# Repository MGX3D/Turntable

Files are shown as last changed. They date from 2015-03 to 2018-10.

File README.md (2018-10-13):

# MGX3D Automatic Turntable

A high precision rotating platform for 100Kg/250lbs typical loads.

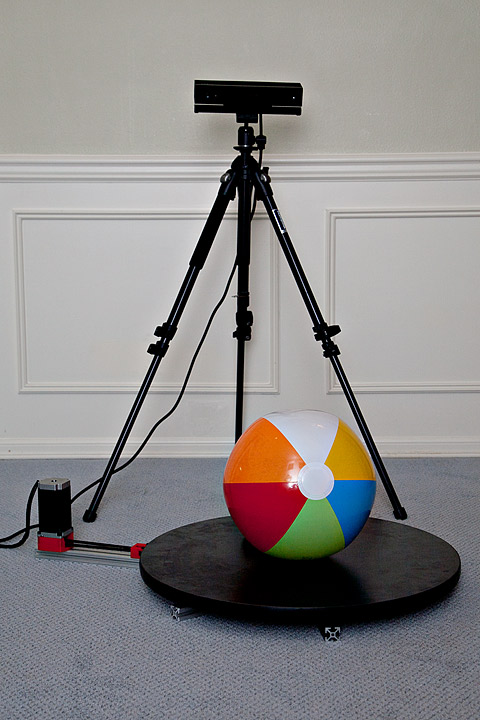
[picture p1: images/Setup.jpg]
Kinect Scan View 3D Scanner view


Description:
------------
This platform was initially designed to automate 3D scanning of people and objects with Kinect v2 and 3D Builder:
- heavy duty: hold a heavy person or average couple, run for 12+ hours non-stop
- powerful drive: spin the person fast enough to avoid scanning artifacts due to movement, breathing, ICD, etc.
- precise rotation: stepper controlled (and USB connected) to experiment with line scanners and algorithms
- low profile: close to the ground increase stability when stepped on
- easy to build: use very few parts that are easy to source
     
The current design has completed more than 2500 scans of people to date, with a typical scan taking only 30 seconds.

Characteristics (typical):
--------------------------
- platform diameter: 500mm (2ft) 
- speed: 0-3 RPM (peripheral speed: 25-50mm/s)
- platform load: up to 300lbs
- resolution: 0.02mm for 450mm OD object (20 arcseconds)

Parts required:
---------------
Warning: not final, might be incomplete. Please be prepared to make adjustments. Unless otherwise noted, eBay/Amazon is a good source for parts.

| Count | Price | Description |
|---|---|---|
| 1x | $40 | 450mm Lazy Susan Aluminum Bearing 500 lbs Turntable Bearings (VXB Brand)|
| 1x | $30 | Stepper motor driver: DM420A. Alternative: HY-DIV268N-5A|
| 1x | $55 | NEMA23, torque: 25 Kg cm (350 oz. in) (example: Wantai 57BYGH115-003 / 3.0A, but many others work here). Alternative is a NEMA17 planetary gear motor (not for Fusion scans!)|
| 4x |  $4 | M5 30mm socket head screws - for the NEMA23 motor mount. Alternative: M4 >35mm and nuts|
| 1x |  $6 | MXL aluminum pulley 40T 8mm bore (anything between 20T and 40T works - bore has to match the motor. GT2 also works)|
| 1x | $10 | 962MXL Timing Belt, .080" Pitch, 77" Outer Circle, 1/4" Wide (McMaster 1679K686, alternative 3/16" 1679K685)|
| 4x |  $3 | F623ZZ: 3x10x4mm flanged bearing for the belt tensioner. Likely to be upgraded to F634zz|
| 2x |  $1 | M3 20mm with 1 nut and 2 washers each. Holds the bearings in the belt tensioner (will be M4 for F634zz)|
| 1x |  $0 | 3D printed part for the NEMA23 mount (STLs in the CAD folder: https://github.com/MGX3D/Turntable/blob/master/CAD/3d_scanner_nema23.stl)|
| 1x |  $0 | 3D printed part for the belt tensioner (STLs in the CAD folder: https://github.com/MGX3D/Turntable/blob/master/CAD/3d_scanner_belt_tensioner.stl)|
| 1x | $20 | Teensy 2.0. Alternative: any Pulse/Dir/Enable capable electronics (examples: Arduino w/ RAMPS shield and shim from Pololu to DM420A or Raspberry Pi 2 with Windows 10 using GPIO pins, etc)|
| 1x | $20 | 1" 8020 72" aluminum extrusion (1010 profile). Will need to be cut in 32"+20"+20". Alternative: metric t-slot extrusion of 20mm or larger|
| 4x |  $4 | 1/4-20 1/2" pan head screws and t-slot nuts - attach the printed parts (motor mount and tensioner) to the aluminum extrusion. Alternative: use M4-12mm + t-nuts|
| 6x |  $5 | M4 16mm screws + t-slot nuts (Can use 8-24 t-slot nuts,  part number 3275 at 8020.inc). Mounts the bearing to the 8020 extrusion|
| 6x |  $1 | #6-1" wood screws - mounts a wooden platform to the bearing. Alternative - double sided tape|
| 1x |  $1 | 2+ meters (6+ feet) of 6 wire cable to transmit signal: low voltage: Enable/Pulse/Direction/Ground (3.3-5vcc) and 12V DC power to the stepper controller. Good fit: network cable with 2 pairs of wires for motor power|
| 1x | $40 |  24" (500mm) disc platform. For 3d scanning of people: preferably 1" thick plywood. Alternative: 1 in. x 24 in. x 2 ft. Pine Edge Glued Panel Round Board at Home Depot (paint or cover with no-slip tape). For other uses: polycarbonate or tempered glass (>3/8", heavy!) or 3/8"-1/2" aluminum disc|
| 12x |  $1 | Optional: M4 washers - only needed if the lazy susan bearing is not offset (inside vs outside rings), example VXB bearings|

--
Approximate total cost: **$250**
Estimated total parts: 37-49

Additional tools required for assembly: 
   - drill with 4mm and 7mm drills. Hand drill works, drill press is better.
   - metric hex/allen keys for metric M3, M4 and M5 screws (m5 works for SAE 1/4" too)
   - saw for the aluminum extrusion. Hand saw works, table saw is better.

Assembly Instructions:
----------------------
The movement in this platform is a quite unique: the belt goes directly from the 40T motor pulley to the big lazy susan bearing, through a bi-lateral belt tensioner. This simple arrangement works incredibly well in practice as it achieves a zero backlash 18:1 typical reduction at a very low cost. The bearing does not need teeth: due to its very large diameter it achieves zero slip through friction. The incidence angle of the belt is gentle enough to not damage the teeth.

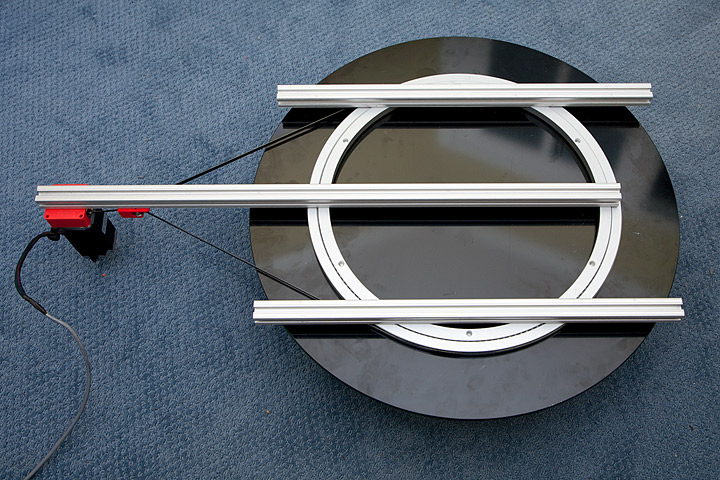
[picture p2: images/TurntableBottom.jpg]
Turntable Bottom View Bottom view


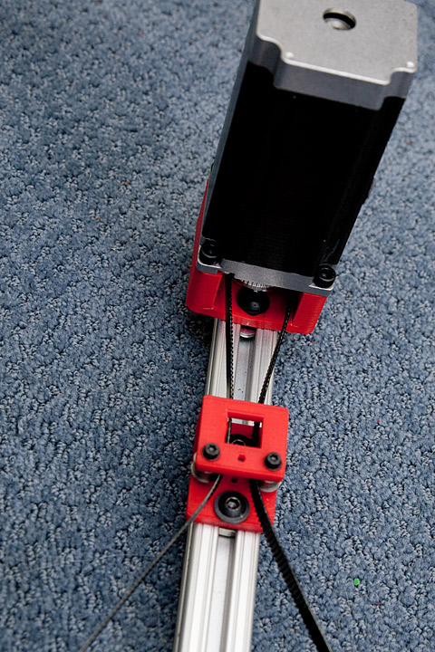
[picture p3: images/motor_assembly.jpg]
Movement View Movement view


The belt is tensioned by sliding the tensioner towards the  bearing. The tensioner also functions as a vertical guide for the belt. 

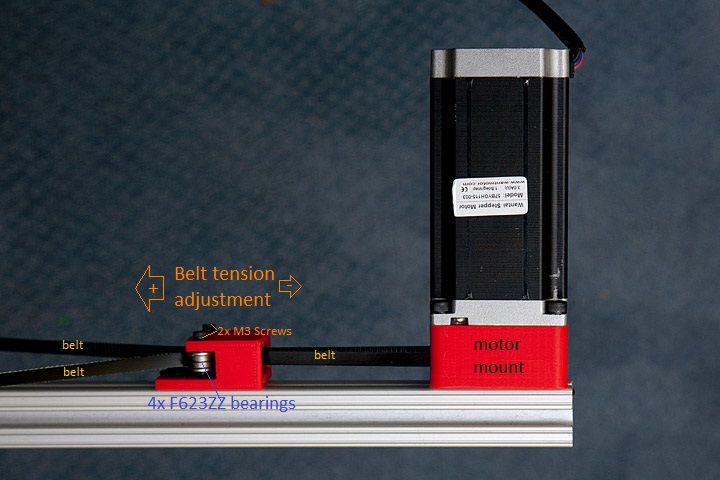
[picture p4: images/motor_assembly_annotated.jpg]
Motor Assembly View Motor assembly


The motor attaches to the extrusion using the 3d printed mount. In the latest design, the motor mount design has been updated to allow easy repositioning of the motor as well as to increase the strength (the 3D model looks slightly different than the pictures below). The holes that take the M5 screws from the motor are designed to be tapped (M5 tap), if you don't have one you can simply use longer M4 screws and nuts on the other side, there is enough clearance.

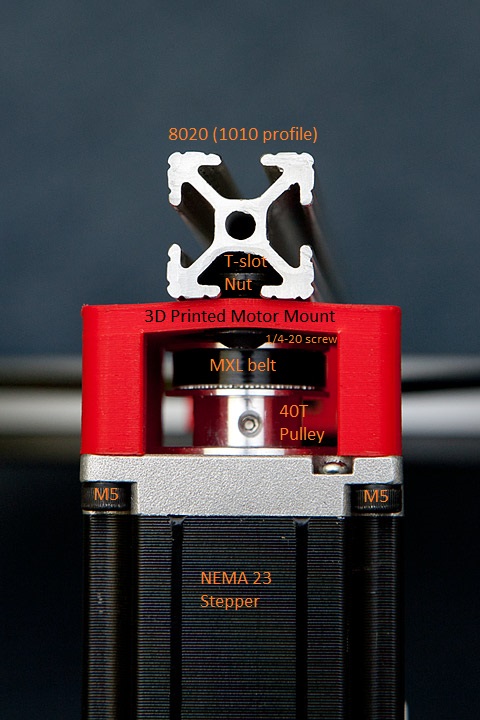
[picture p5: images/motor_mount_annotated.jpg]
Motor Mount View Motor mount


The lazy susan bearing is attached directly to the aluminum extrusion by drilling 12 through holes, 4mm diameters: 6 holes in the inside ring and 6 holes in the outside ring. The bearings are usually half-way drilled from the factory, those holes work well as a guide. Two drilling operations are required, one through hole the screw itself (4 - 4.25mm dia drill) and a secondary hole one for the screw socket-head cap (7mm dia drill but only 4mm deep!). The screw socket heads need to be sunk so they don't block the rotation of the bearing - this is needed even if the bearing is offset (the offset is typically 1-2mm). Alternatively, one can use 3D printed raisers with M4 pan head screws. If the bearing rings are not vertically offset (typical for VXB bearings) you will need to insert M4 washers between the bearing and the extrusion to eliminate friction.

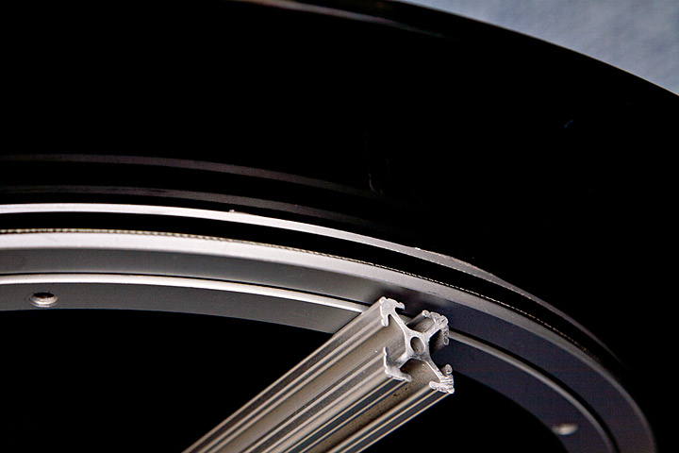
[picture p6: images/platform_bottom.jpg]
Bottom View Bottom view


After the bearing is attached to the extrusion (and the belt tension is roughly correct) the round platform is attached to the bearing with 6 pcs of #6-1" wood screws (and washers). An option here is to use double sided adhesive tape (red in the image), however once mounted like this it won't be possible to access to the screws that go into the extrusion. Double sided tape is however the only option for tempered glass platforms (pictured). The challenging part here is to get the bearing perfectly centered on the platform, the trick is to find the center of the disk and then draw a circle that matches the bearing outside diameter.

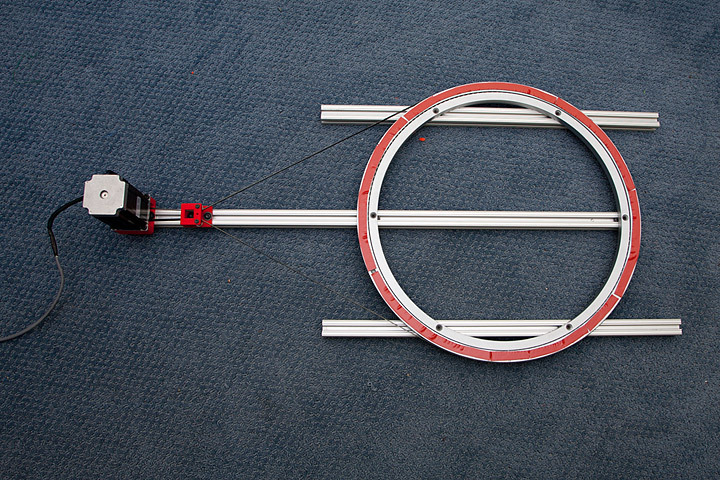
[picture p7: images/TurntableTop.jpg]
Turntable Top View Top view


Possible applications:
---------------------
- 3D scanning of people - using Kinect v2 and 3D Builder 
- 3D scanning of objects - using laser line scanners
- Rotary axis for CNC machining or 3D Printing
- Showroom displays for heavy objects
- Automatic tool changer for CNCs
- Cake decoration?
- ... and more

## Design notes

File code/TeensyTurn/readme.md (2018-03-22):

# TeensyTurn

This shows an example controller running on Arduino Teensy 2.0 (Teensyduino)

Wiring:
-------
The code is configured for Teensy 2.0 / Teensyduino - it maps pins 19,20 and 21 to Step/Direction and respectively Pulse on the controller.

To compile:
----------
1. Install Arduino 1.0.6 or equivalent (http://www.arduino.cc)
2. Install Teensyduino 1.23 or newer (http://www.pjrc.com/teensy/td_download.html)
3. Load the sketch in Arduino
  - Set board type to "Teensy 2.0" or your equivalent
  - Set USB Type to "Raw HID"
  - Click 'Verify'. At this point Arduino should start the Teensy firmware upload app.
  - Reset Teensy - the app should flash it. 
  - Tweak the parameters as needed and repeat the last two steps 
4. Start Serial Monitor and connect at 9600 baud. You should see a message like "MGX3D Turntable v1.00 Initialized"

Usage:
--------
To test the controller, connect to the Teensyduino with raw_hidtest.exe (https://www.pjrc.com/teensy/rawhid.html), 

1. Press number keys 1-5 to select 
the stepper control parameters:
    - nSteps - The number of steps (or microsteps) to issue
    - lhDelay - delay (microseconds) between Low-High transitions (example: feed rate)
    - hlDelay - delay (microseconds) between High-Low transitions (example: minimum impulse)
    - accRamp - slope length (impulses) for acceleration/deceleration
    - accBeta - slope angle (delay) for acceleration/deceleration
2. Press '+' or '-' to increase or decrease the parameters as needed 
3. Press 'r' key to issue a move command. If you connect with the Serial Monitor in Arduino and should see the following:
    "
        MGX3D Turntable v1.00 Initialized
        [...]
        Depth data sentReceived packet, command=114 param1=0 param2=0 param3=0 wparam1=0 wparam2=0
        RUN:  steps=600 LHus=432 HLus=5 accRamp=79 accBeta=41
    "

To run the controller with specific parameters, send a 64-byte buffer in the folllwing format:

    Offset  Type        Meaning
    ------  ----        -------
    0x00    byte        always 0x00 
    0x01    byte[3]     reserved
    0x04    uint16      nSteps
    0x08    uint16      lhDelay
    0x0C    uint16      hlDelay
    0x10    uint16      accRamp
    0x14    uint16      accBeta

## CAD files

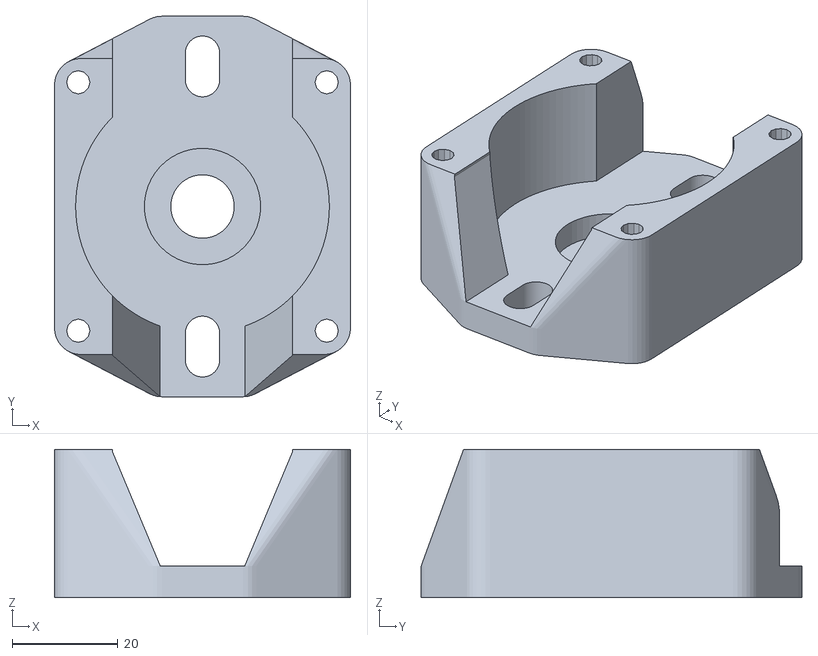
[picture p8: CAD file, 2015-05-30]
CAD/3d_scanner_nema23.stl
56.0 x 72.0 x 28.0

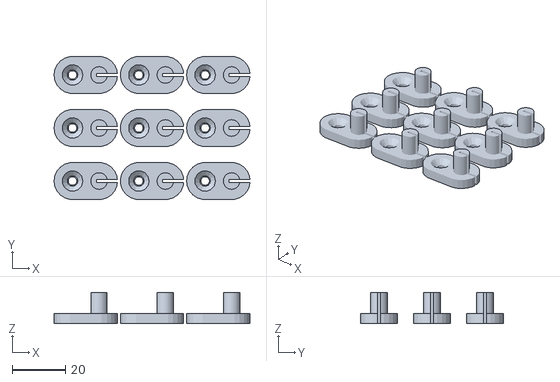
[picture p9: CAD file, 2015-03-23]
CAD/3d_scanner_spacers.stl
73.9 x 53.9 x 11.8

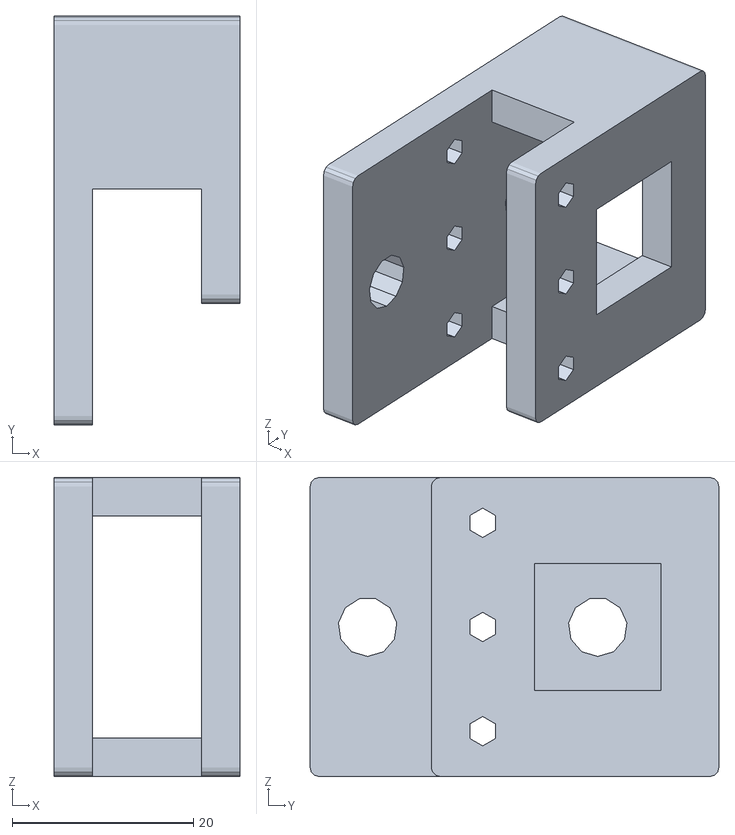
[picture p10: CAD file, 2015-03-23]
CAD/3d_scanner_belt_tensioner.stl
20.5 x 45.1 x 33.0

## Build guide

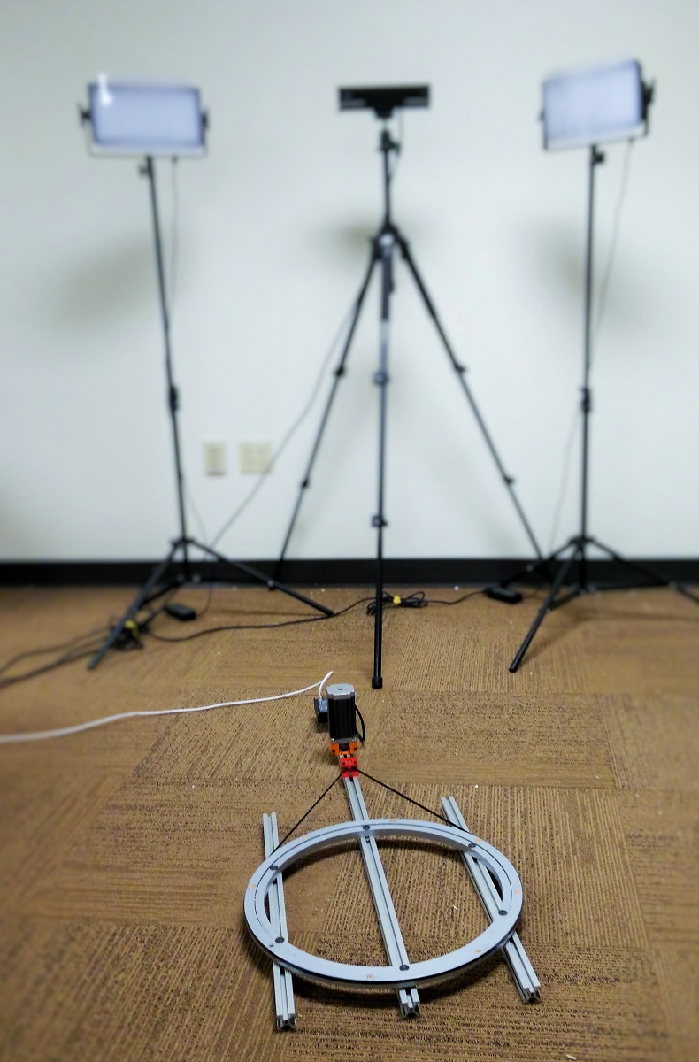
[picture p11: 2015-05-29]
images/TurntableSetup.jpg

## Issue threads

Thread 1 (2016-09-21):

Timing belt choice

lee7670, 2016-09-21:
Any reason you're using a GT2 Pulley and a MXL Belt for this?

MGX3D, 2016-10-07:
Good catch :). This is more as a result of the parts I had on hand at the time. Turned out to work really well in practice though, after >1 year of use the wear on the belt turns out to be on the edge instead (caused by drift coming from the alignment of the pulley-tensioner-bearing). Using a matching MXL pulley here is definitely a better choice (a GT2 setup should work equally well, the bearing contact surface is large enough for the more rounded tooth profile to not matter).

Closed 2016-10-07.

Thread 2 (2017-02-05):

Did somebody try to rebuild it in europe?

DominicBoettger, 2017-02-05:
As there are lot of products not available in the "metric" world. I asked myself if somebody found suitable products and dimension for the rest of the world.

MGX3D, 2017-02-05:
Most of the parts are in the metric system, a few that have escaped are not at all critical to the design or function. For example the extrusion or screws - replace them with similarly sized metric parts, the design is simple enough to scale and flexible enough to adjust over wide ranges (example belt size, extrusion size, etc).

DominicBoettger, 2017-02-05:
Thanks a lot. I will have a look for a similar Aluminium extrusion. I will try it.

ashenkin, 2018-02-23:
Hey @DominicBoettger , I'm in the UK, and interested in building one too. Wondering if you found the parts in europe? thanks...

Closed 2017-02-05.

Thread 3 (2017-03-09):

Steppermotor - Hardware

sjeesflix, 2017-03-09:
Hello,

Im trying to replicate the project you did, but I don't have a lot of experience with electronics and programming. In the code you provide, you adres 5 pins for configuration for the teensy 2.0. I guess stepPin goes into PUL, enblPin goes into ENBL and dirPin goes into DIR from the DM420A? This leaves me with 2 pins: readoutPin and triggerPin.

With pinMode(readoutPin, INPUT); you set this pin to input and with pinMode(triggerPin, INPUT_PULLUP); you set this pin to input as well, only with a pull up resistor

I don't really know what to do with these pins. Obviously I should implement some kind of button/switch, but I don't know how? Can you please provide me with some information?

Thanks in advance!!

PS: Nice project! very cool

MGX3D, 2017-04-29:
triggerPin is a NC (normally closed) switch, this is to trigger a rotation on click (or step-by-step if you keep it pressed). GPIO1 is right next to GND on ESP8266, so you can just solder a microswitch in place there.
readoutPin was reserved for a sensor, but is not used anywhere, ignore it.

Closed 2017-04-29.

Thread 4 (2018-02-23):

RaspPi for photogrammetry automation

ashenkin, 2018-02-23:
Thanks so much for this great writeup.  I'm interested in putting together a system to automate photogrammetry.  So, the idea would be to program the system to rotate x degrees, then trigger a camera, then rotate again, another photo, etc.  I suspect that a raspberry pi (or laptop) might be a bit more flexible than an arduino in terms of making complex automation happen.  I'm wondering if you might have any thoughts about this?  Think the arduino would be replaced by the rpi, or perhaps just have the rpi controlling the arduino?

thanks again...

MGX3D, 2018-02-24:
Definitely possible to use raspberry pi just by itself to control the stepper as well as add additional stuff, I didn't have time to try it myself but it should work. In fact, for a newer version of this (which I haven't published yet) I've used an ESP8266 to expose:
- REST APIs over WiFi and equivalent USB commands for low latency stepping
- stepper control
- a line laser on/off
all in one $7 board. ESP32 would make it even more interesting (BlueTooth, etc).

ashenkin, 2018-02-26:
Very slick.  Thanks for the info - i'll ping you if i end up implementing this!

Closed 2018-03-14.

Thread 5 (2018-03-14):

stepper model

ashenkin, 2018-03-14:
hi there,
i'm having an issue finding an NMEA 23 stepper with the specified torque that comes in under the 2A that the DM420A driver can handle.  Wondering if you might share the specific stepper you used?  I'll look for the alternative driver you spec'd, but still curious about the stepper model...  Thanks...

MGX3D, 2018-03-19:
Specific model I used Wantai 57BYGH115-003, but many others work here.
Note: The stepper should have higher current rating than the driver, and note DM420A as peak 2.83A.

ashenkin, 2018-03-19:
Thanks for the reply.  I picked up a Motech MT-2315HS300AW (http://www.motechmotor.com/products_detail.php?id=159&cid=&page=3), 3A/phase.  The HY-DIV268N-5A is more readily available than the DM420A here.  Do you think its 5A rating would make it risky to use with a stepper rated to 3A?  I can sniff around for other options if so...

ashenkin, 2018-03-20:
nevermind - i see there are dip switches for the current.  anyway, i'm picking up a TB6600 as they're readily available here... will try to update with a parts list from europe once i've built and tested...

Closed 2018-03-20.

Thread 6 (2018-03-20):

What are you using for your DC supply to the driver?

ashenkin, 2018-03-20:
I'm trying to build a system that can run on a 12V battery, but curious about your setup here.

Closed 2018-03-22.

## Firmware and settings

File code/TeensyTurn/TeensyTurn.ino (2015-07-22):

/*

        MGX3D 3D Scanning Turntable Controller


Copyright (c) 2015, Marius Gheorghescu. All rights reserved.

mariusg (at) live.com / www.mariusg.com / www.github.com/mgx3d/


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
1. Redistributions of source code must retain the above copyright 
notice, this list of conditions and the following disclaimer.

2. Redistributions in binary form must reproduce the above copyright 
notice, this list of conditions and the following disclaimer in the 
documentation and/or other materials provided with the distribution.

3. Neither the name of the copyright holder nor the names of its contributors
may be used to endorse or promote products derived from this software without
specific prior written permission.

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
*/


// pinout configuration for Teensy 2.0
int stepPin = 19;
int enblPin = 21;
int dirPin = 20;
int readoutPin = 17;
int triggerPin = 1;

// test rotation: 300rpm (5rps, pulse at rougly 1-16Khz), assume 20:1 reduction
unsigned int turnFactor=40;
unsigned int speedFactor=4;
unsigned int lhDelayFactor=21;
unsigned int hlDelayFactor=21;
unsigned int accRampFactor=64;
unsigned int accRampBeta=32;

int paramSlot=0;

// RawHID packets are always 64 bytes
byte buffer[64];

void setup()
{
  pinMode(stepPin, OUTPUT);
  pinMode(enblPin, OUTPUT);
  pinMode(dirPin, OUTPUT);

  pinMode(readoutPin, INPUT);
  
  digitalWrite(enblPin, HIGH);
  digitalWrite(dirPin, HIGH);
  
  pinMode(triggerPin, INPUT_PULLUP);
  
  Serial.begin(9600);
  Serial.println(F("MGX3D Turntable v1.00 Initialized"));
}

void run_motor(int doIO, unsigned int nSteps, unsigned int lhDelay, unsigned int hlDelay, unsigned int accRamp=0, unsigned int accBeta=0)
{
  
  if (doIO) {
    
    for (int i=0; i<64; i++) {
        buffer[i] = 0;
    }
    
    Serial.print(F("RUN: ")); 
    
    Serial.print(F(" steps=")); Serial.print(nSteps);  
    Serial.print(F(" LHus=")); Serial.print(lhDelay);
    Serial.print(F(" HLus=")); Serial.print(hlDelay);
    Serial.print(F(" accRamp=")); Serial.print(accRamp);
    Serial.print(F(" accBeta=")); Serial.print(accBeta);
         
    Serial.println(F(""));
  }

  // run the motor
  for (unsigned int i=0; i<nSteps; i++) {
    digitalWrite(stepPin, HIGH);
    delayMicroseconds(hlDelay);
    digitalWrite(stepPin, LOW);
    
    if (digitalRead(triggerPin) == LOW) {
      // stop - the button pressed again, energency stop      
      delay(250);
      // return right away, do not decelerate
      return;
    }
    
    if (i<accRamp) {
      // accelerate
      //Serial.println((accRamp-i)*accBeta);
      delayMicroseconds(lhDelay + (accRamp-i)*accBeta);
    } else if (i > (nSteps - accRamp)) {
        // decelerate
      //Serial.println((i-nSteps + accRamp)*accBeta);
      delayMicroseconds(lhDelay + (i-nSteps + accRamp)*accBeta);
    } else {
      delayMicroseconds(lhDelay);
    }
  }

  if (doIO) {
    // measure
    for(int i=0;i<32;i++) {
        int val = analogRead(readoutPin);
        buffer[i*2] = highByte(val);
        buffer[i*2 + 1] = lowByte(val);      
    }
    
    // send data      
    int n = RawHID.send(buffer, 100);
    if (n > 0) {
        // Serial.println(F("Depth data sent"));
    } else {
        Serial.println(F("Unable to transmit packet"));
    }
  }

}

void loop() 
{
  int n = RawHID.recv(buffer, 0); // 0 timeout = do not wait
  if (n > 0) {
    // the computer sent a message.
    Serial.print(F("Received packet, command="));
    Serial.print((int)buffer[0]);

    // HL delay
    Serial.print(F(" param1="));
    Serial.print((int)buffer[1]);

    // LH delay
    Serial.print(F(" param2="));
    Serial.print((int)buffer[2]);

    // acceleration beta factor
    Serial.print(F(" param3="));
    Serial.print((int)buffer[3]);

    // steps
    Serial.print(F(" wparam1="));
    Serial.print(*(int*)&buffer[4]);    

    // acceleration ramp steps
    Serial.print(F(" wparam2="));
    Serial.print(*(int*)&buffer[8]);

    Serial.println("");
    
    switch (buffer[0])
    {
    case 0x00:
      // paramer rotation
      run_motor(*(unsigned int*)&buffer[0x04], *(unsigned int*)&buffer[0x08], 
        *(unsigned int*)&buffer[0x0C], *(unsigned int*)&buffer[0x10], *(unsigned int*)&buffer[0x14]);
      break;

    case '+':
      switch(paramSlot) {
        case 0: 
          turnFactor++;
          break;
          
        case 1:
          lhDelayFactor++;
          break;
          
        case 2:
          hlDelayFactor++;
          break;

        case 3:
          accRampFactor++;
          break;                  

        case 4:
          accRampBeta++;
          break;
          
        case 5:
          speedFactor++;
          break;
      }
      break;
      
    case '-':
      switch(paramSlot) {
      case 0:
        turnFactor = max(1, turnFactor--);
        break;
        
      case 1:
        lhDelayFactor = max(0, lhDelayFactor--);
        break;
        
      case 2:
        hlDelayFactor = max(0, hlDelayFactor--);
        break;

      case 3:
        accRampFactor = max(0, accRampFactor--);
        break;
        
      case 4:
        accRampBeta = max(0, accRampBeta--);
        break;
        
      case 5:
        speedFactor = max(1, speedFactor--);
        break;
        
      }
      break;
      
    case '1':
    case '2':
    case '3':
    case '4':
    case '5':
    case '6':
      paramSlot = buffer[0]-'1';
      break;
    
    case 'r':      
        run_motor(1, turnFactor*200*speedFactor, 8192/(1+pow(1.3,32-lhDelayFactor)), 8192/(1+pow(1.3,32-hlDelayFactor)), accRampFactor*speedFactor, accRampBeta/speedFactor);
        break;
    }
  }  
  
  if (digitalRead(triggerPin) == LOW) {
      delay(250);
      run_motor(0, turnFactor*200*speedFactor, 8192/(1+pow(1.3,32-lhDelayFactor)), 8192/(1+pow(1.3,32-hlDelayFactor)), accRampFactor*speedFactor, accRampBeta/speedFactor);
  }
}

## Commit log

2015-03-23 CAD models
    Motor + tensioner STLs
    [3d_scanner_belt_tensioner.stl, 3d_scanner_nema23.stl]
2015-03-23 Bearing spacers
    [3d_scanner_spacers.stl]
2015-05-24 Motor assembly details
2015-05-24 Additional assembly images
2015-05-30 Stronger motor mount. Improved access to mounting screws. Tighter motor screw holes (for M5 tapping).
    [3d_scanner_nema23.stl]
2015-06-17 Added trigger button
    Added button to start/stop rotation. Parameters default to roughly one
    full rotation in 30 seconds. Added parameter to modify speed.
2015-07-22 No I/O on the hardware trigger, prevent buffers from getting full when running untethered.
    [TeensyTurn.ino]
2015-07-24 Turn on the LED when rotating More pictures.
